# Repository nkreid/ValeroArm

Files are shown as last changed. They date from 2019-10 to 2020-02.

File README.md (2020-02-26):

# ValeroArm
I spent the summer of 2019 building a cost-effective, durable, and versatile tendon-driven arm. The motivation was to build an arm that had planar, universal, and rotational joints on a large scale. This design could then be scaled down to the size of fingers on the hand. We built and modeled a planar, two joint, three muscle system.

# Tendon Routing and Moment Arm Size Optimization
  A large focus was directed toward finding the optimal tendon routing for the arm. This was done in python by maximizing the radius of a circle inside the Feasible Force Set with the circle’s center located at the endpoint. The choice of a circle defined the maximum force the endpoint could exert in all directions. The routes were swept over the anatmical limits of the elbow (-10 degrees,150 degrees) and averaged over the range. This average force production was our metric we used to pick the most versatile route. We defined versatile as “producing the largest force in all directions, for every position.”
  
  For a two joint, three muscle this produces a 2x3 matrix with close to 800 combinations. Each row is a joint and each column is a muscle. The numbers one and negative one were used to denote the direction of angle change that a tendon could produce. Tendons can only act on a joint in one direction because muscles only contract and cannot extend. The possible R matrices were reduced to 14 by the following assumptions: 
    
    1.	Every row needs a positive and negative moment arm to move in both directions.
    2.	The top row cannot contain a zero because the current design of the arm does not 
        allow a tendon to reach the distal  joint without first touching the proximal joint. 
    3.	Matrices with the same columns in different orders are duplicates of each other. 
    
  Out of the 14 matrices, 10 produced numerical results with 2 routes clearly stronger than the rest. These two matrices were “opposites” of each other as shown in FIGURE. This optimal tendon routing is consistent with the routing chosen in (G2P Paper). This information was presented on a poster at the Keck School of Medicine’s summer undergraduate poster symposium. 
	
  The 14 feasible routes were then scaled to allow for moment arm differences between each muscle and joints. The 14 feasible routes were multiplied by almost 2 million scaling matrices by scalar multiplication.  These scaling matrices were all the variations of a 2x3 matrix containing the numbers between 0 and 1 (inclusive) with a 0.1 step (0,0.1,0.2,0.3…). By choosing a maximum of 1.0, these values are normalized by dividing all the values by the arm's largest moment arm. These new matrices were ran through the same optimization procedure as before and the top 100 matrices were kept. The results are as follows:
```
       MATRIX         Average Force Output
[[-1.   0.2  0.9]
 [-0.1 -1.   1. ]]  :: 2.3684792518615723
[[-1.   1.   0.4]
 [-0.6 -0.9  1. ]]  :: 2.369333267211914
[[-1.   0.9  0.4]
 [-0.6 -0.8  1. ]]  :: 2.369748115539551
[[-0.1 -0.9  1. ]
 [-1.   0.3  0.6]]  :: 2.3703784942626953
[[-1.  -0.1  1. ]
 [-1.   0.9  0.1]]  :: 2.3703880310058594
[[-0.1 -1.   1. ]
 [-1.   0.2  0.9]]  :: 2.3708009719848633
[[-1.   1.   0.1]
 [-1.  -0.5  1. ]]  :: 2.373188018798828
[[-0.1 -1.   1. ]
 [-1.   0.3  0.6]]  :: 2.376481533050537
[[-1.  -0.1  1. ]
 [-1.   1.   0.1]]  :: 2.3765554428100586
[[-1.   0.9  0.1]
 [-0.8 -0.5  1. ]]  :: 2.377281665802002
[[-1.   1.   0.2]
 [-0.8 -0.3  1. ]]  :: 2.377704620361328
[[-1.   0.1  1. ]
 [-0.1 -1.   0.9]]  :: 2.3780016899108887
[[-1.   0.1  1. ]
 [-0.2 -0.9  1. ]]  :: 2.3781371116638184
[[-1.   1.   0.2]
 [-0.6 -0.6  1. ]]  :: 2.37845516204834
[[-0.1 -1.   1. ]
 [-1.   0.3  0.7]]  :: 2.3785605430603027
[[-0.1 -0.9  1. ]
 [-1.   0.   0.9]]  :: 2.378894805908203
[[-1.   0.8  0.2]
 [-0.8 -0.4  1. ]]  :: 2.378972053527832
[[-1.   1.   0.2]
 [-0.8 -0.5  1. ]]  :: 2.378972053527832
[[-1.   1.   0.2]
 [-0.7 -0.4  1. ]]  :: 2.380239963531494
[[-1.   0.8  0.2]
 [-0.8 -0.3  1. ]]  :: 2.380913734436035
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
```

It is interesting to note that our best routes are not all ones and zeros as initially expected. However, the top 5 results are all very similar with minor deviations.

# Physical Design and Construction
  The first design of the arm was constructed together with Paris Hijali. It was made out of PVC and 3D printed components. While it was a solid proof of concept, there were many problems that arose. I addressed many of these problems in the second version. 
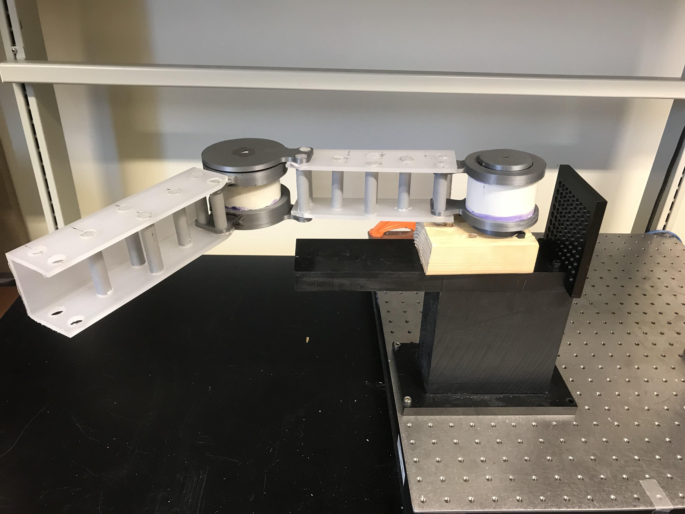
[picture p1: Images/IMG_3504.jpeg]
PVC Arm


  Version 2 was created using very modular parts which allowed for the arm to be modified depending on the task. Most of the parts were ordered from McMaster or ServoCity. This version of the arm included a planar elbow and shoulder joint along with a rotational pronation/supination joint in the forearm. At the end of the arm, there were three versions of a wrist-- ranging from zero to the two degrees of freedom that a real wrist has. We constructed the version with zero DOFs for the first phase of testing. The current hand we were using in the lab was underactuated and driven by two servos. There was a cavity created in the distal forearm to house the two servos needed to drive the hand. 
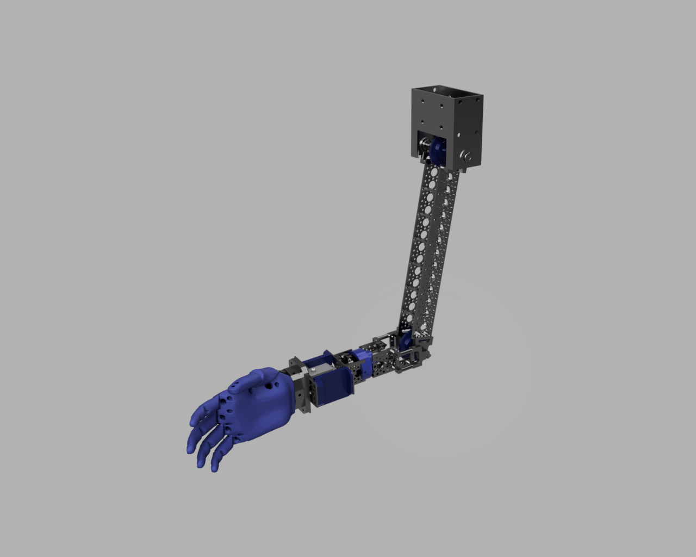
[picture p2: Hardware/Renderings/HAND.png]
Modular Arm
 

  We designed a multi-moment-arm (MMA) for a planar joint. It allowed multiple tendons to pass over the same joint with different moment arms. If I were to experimentally test the optimization that I presented above, I would create different MMA according to different routes. I would then put the endpoint of the arm into a device to measure the force. I could then sweep the elbow joint and measure the forces in different postures to see if it supports the data derived theoretically. 
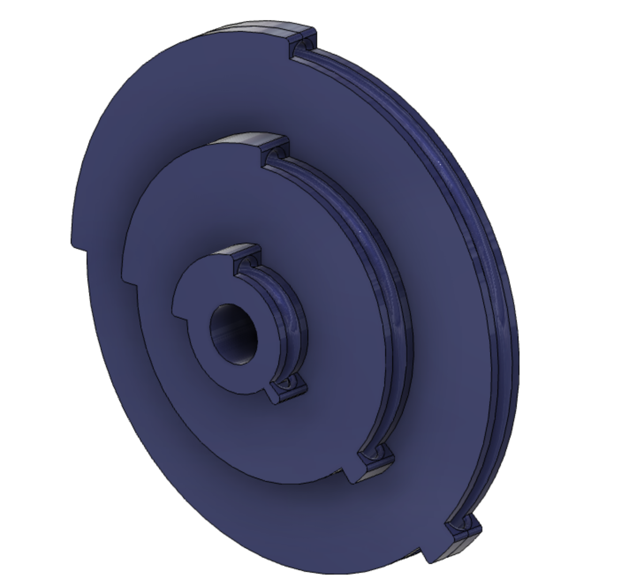
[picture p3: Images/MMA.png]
MMA


# Future Directions
All the code is linked on the GitHub for this page at https://github.com/nkreid/ValeroArm
In addition, all the CAD files are available on Fusion 360 under the project title 'HAND - BBDL'
If you need access to either please ask Suraj or Koby.

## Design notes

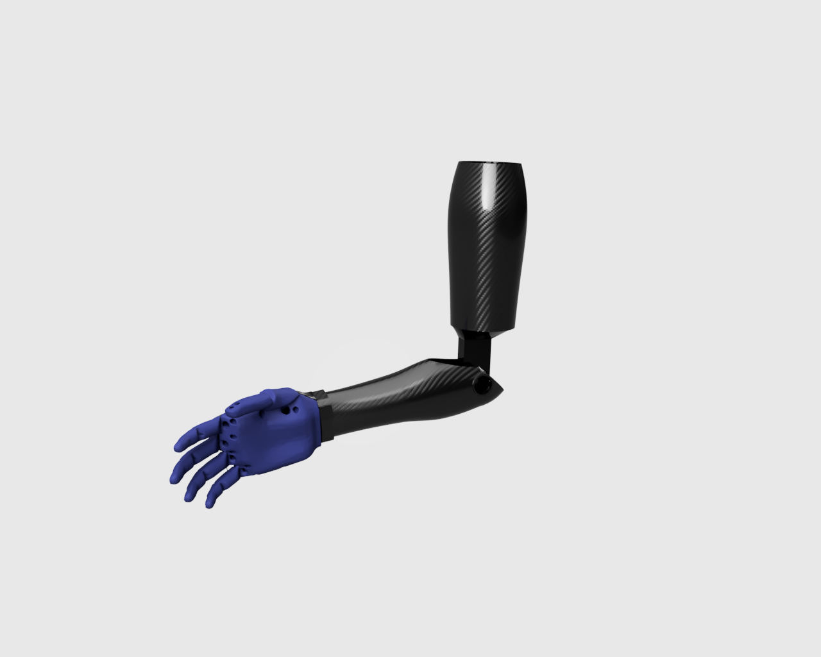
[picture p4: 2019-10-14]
Hardware/Renderings/Prosthetic/Custom_Forearm_2019-Jul-27_07-30-07PM-000_CustomizedView183382668_png.png

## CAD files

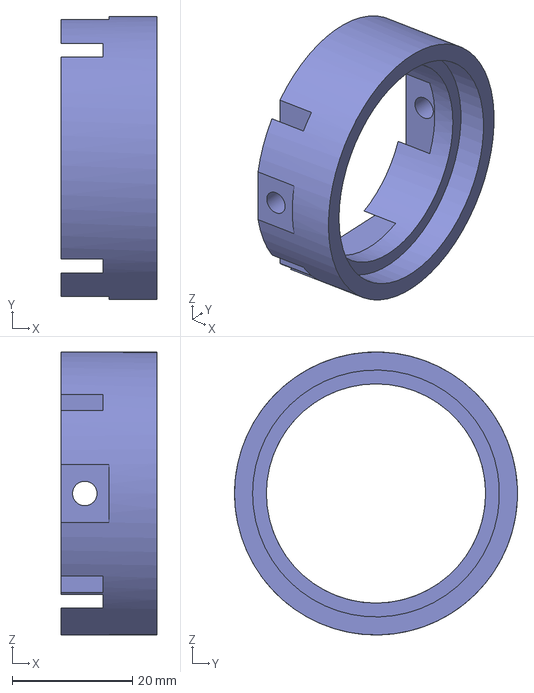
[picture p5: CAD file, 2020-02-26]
Hardware/Fusion Files/Rotation Joint_Outer Sleeve v1.step
16.0 x 47.0 x 47.0 mm

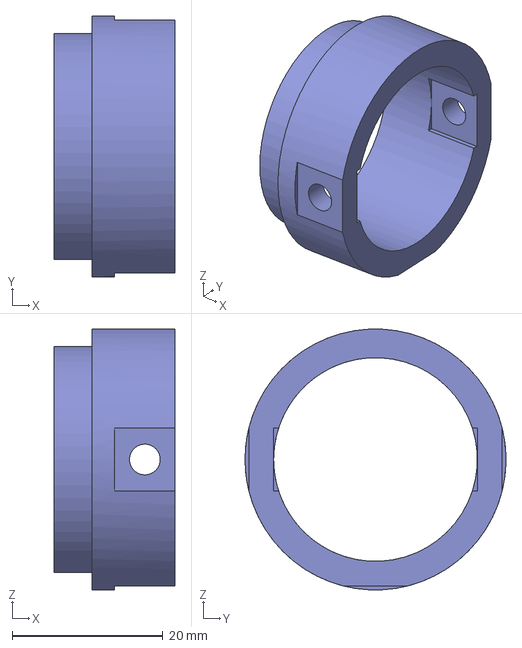
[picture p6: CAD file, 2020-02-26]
Hardware/Fusion Files/Rotation Joint_Inner Sleeve v1.step
16.0 x 34.6 x 34.5 mm

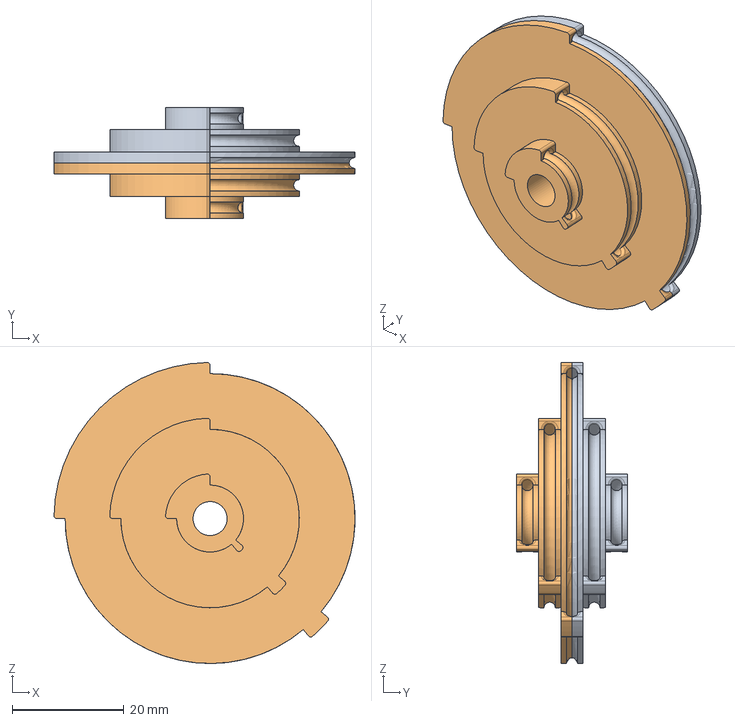
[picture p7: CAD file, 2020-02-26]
Hardware/Fusion Files/Multi Moment Arms (MMA) v5.step
54.0 x 20.0 x 54.0 mm

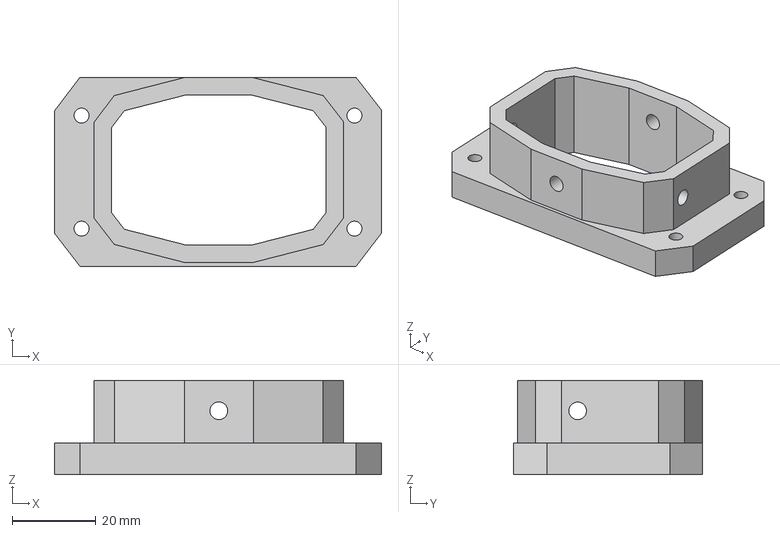
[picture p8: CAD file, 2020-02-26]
Hardware/Fusion Files/R_Ada_v1.1_Back_Cover_Hand Adapter v3.step
77.9 x 45.0 x 22.5 mm

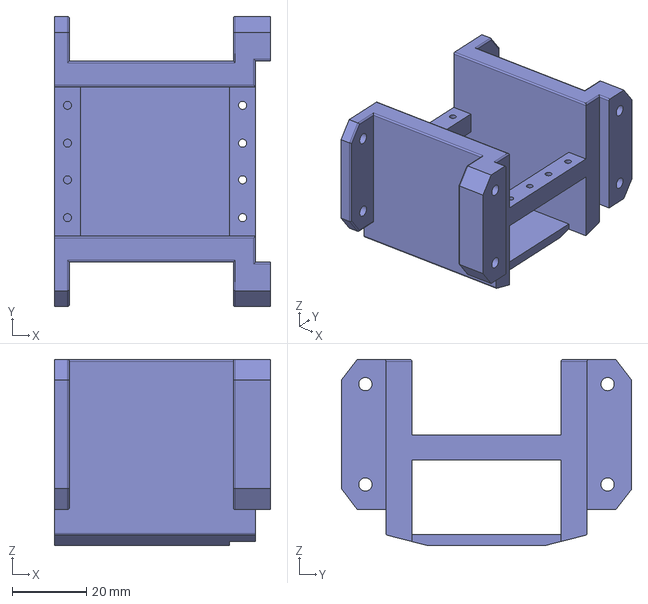
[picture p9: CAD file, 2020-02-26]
Hardware/Fusion Files/HAND v2_Servo Holder v3.step
58.0 x 77.9 x 50.0 mm

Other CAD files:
Hardware/Fusion Files/HAND v2_Servo Holder v3.f3d
Hardware/Fusion Files/Multi Moment Arms (MMA) v5.f3d
Hardware/Fusion Files/R_Ada_v1.1_Back_Cover_Hand Adapter v3.f3d
Hardware/Fusion Files/Rotation Joint_Inner Sleeve v1.f3d
Hardware/Fusion Files/Rotation Joint_Outer Sleeve v1.f3d

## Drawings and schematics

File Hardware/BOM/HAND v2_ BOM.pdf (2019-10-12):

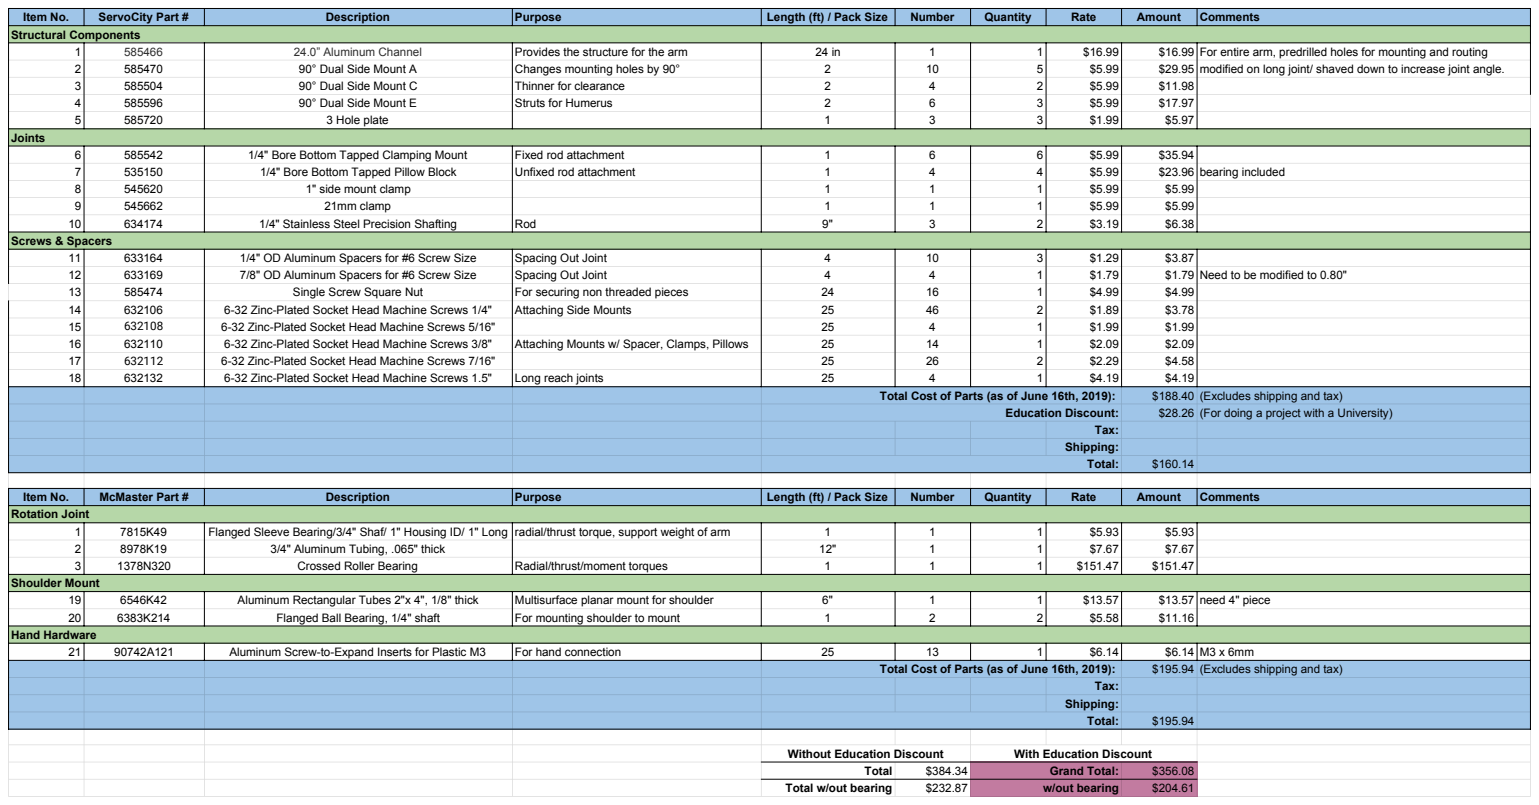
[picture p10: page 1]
Item No.; ServoCity Part #; Description; Purpose; Length (ft) / Pack Size; Number; Quantity; Rate; Amount; Comments; Structural Components; 24.0” Aluminum Channel; Provides the structure for the arm; For entire arm, predrilled holes for mounting and routing; 90° Dual Side Mount A; Changes mounting holes by 90°; modified on long joint/ shaved down to increase joint angle.; 90° Dual Side Mount C; Thinner for clearance; 90° Dual Side Mount E; Struts for Humerus; 3 Hole plate; Joints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

Humerus | | Proximal Forearm | short | long
Channel | 10.4" | 90° Dual Side Mount A | 4 | 4

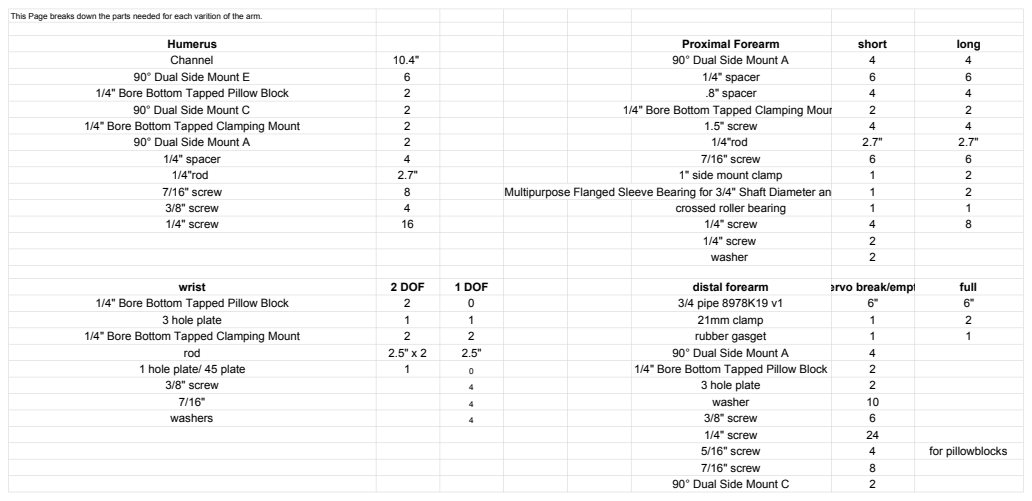
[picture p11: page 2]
90° Dual Side Mount E; 1/4" spacer; 1/4" Bore Bottom Tapped Pillow Block; .8" spacer; 90° Dual Side Mount C; 1/4" Bore Bottom Tapped Clamping Mount; 1.5" screw; 90° Dual Side Mount A; 1/4"rod; 7/16" screw; 1" side mount clamp; Multipurpose Flanged Sleeve Bearing for 3/4" Shaft Diameter and 1" Housing ID, 1" Long 1; 3/8" screw; crossed roller bearing; 1/4" screw; washer; wrist; 2 DOF; 1 DOF; distal forearm; servo break/empty; full; 3/4 pipe 8978K19 v1; 3 hole plate; 21mm clamp; rubber gasget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

This Page breaks down the parts needed for each varition of the arm.

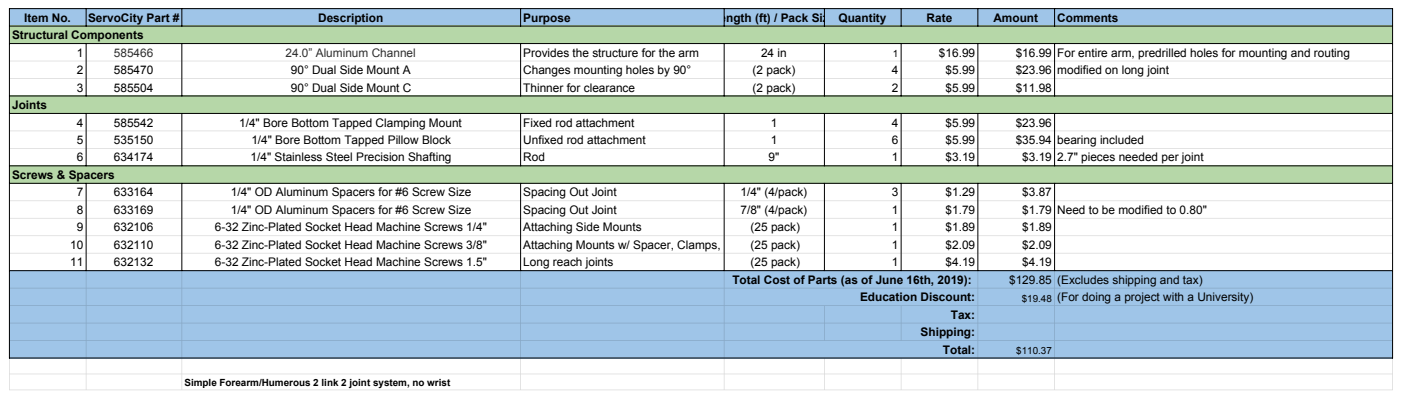
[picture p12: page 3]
Item No.; ServoCity Part #; Description; Purpose; Length (ft) / Pack Size Quantity; Rate; Amount; Comments; Structural Components; 24.0” Aluminum Channel; Provides the structure for the arm; For entire arm, predrilled holes for mounting and routing; 90° Dual Side Mount A; Changes mounting holes by 90°; (2 pack); modified on long joint; 90° Dual Side Mount C; Thinner for clearance; Joints; 1/4" Bore Bottom Tapped Clamping Mount; Fixed rod attachment; 1/4" Bore Bottom Tapped Pillow Block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

Simple Forearm/Humerous 2 link 2 joint system, no wrist

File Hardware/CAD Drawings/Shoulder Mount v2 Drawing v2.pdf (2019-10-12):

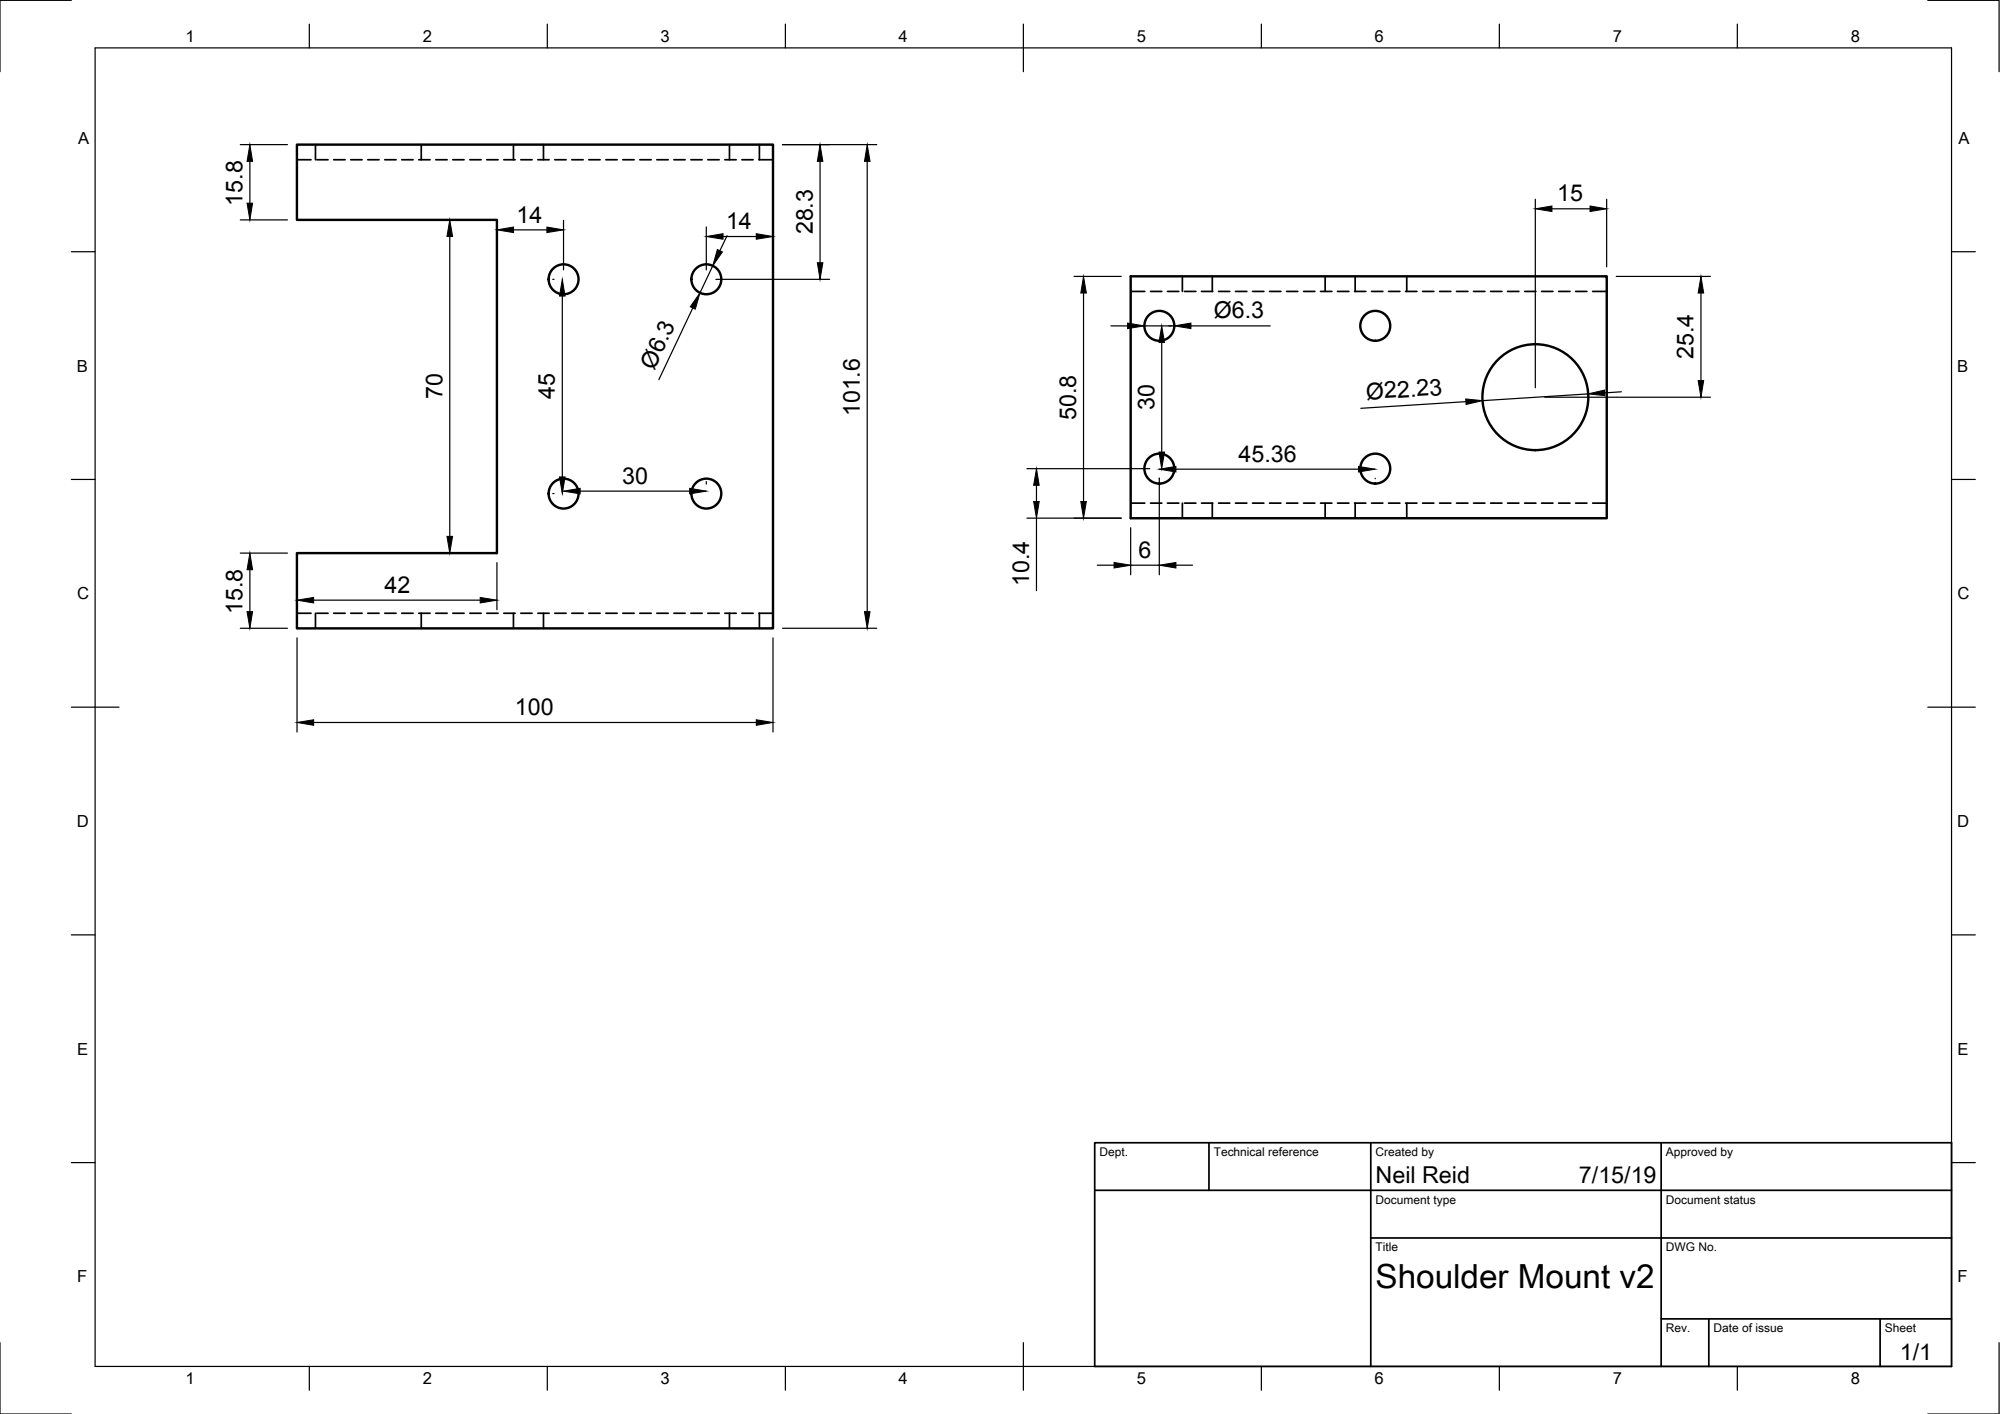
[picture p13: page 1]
Neil Reid 101.6

Dept. | Technical reference | Created by 7/15/19 | Approved by

Document type | Document status

Title Shoulder Mount v2 | DWG No.

Rev. | Date of issue | Sheet 1/1

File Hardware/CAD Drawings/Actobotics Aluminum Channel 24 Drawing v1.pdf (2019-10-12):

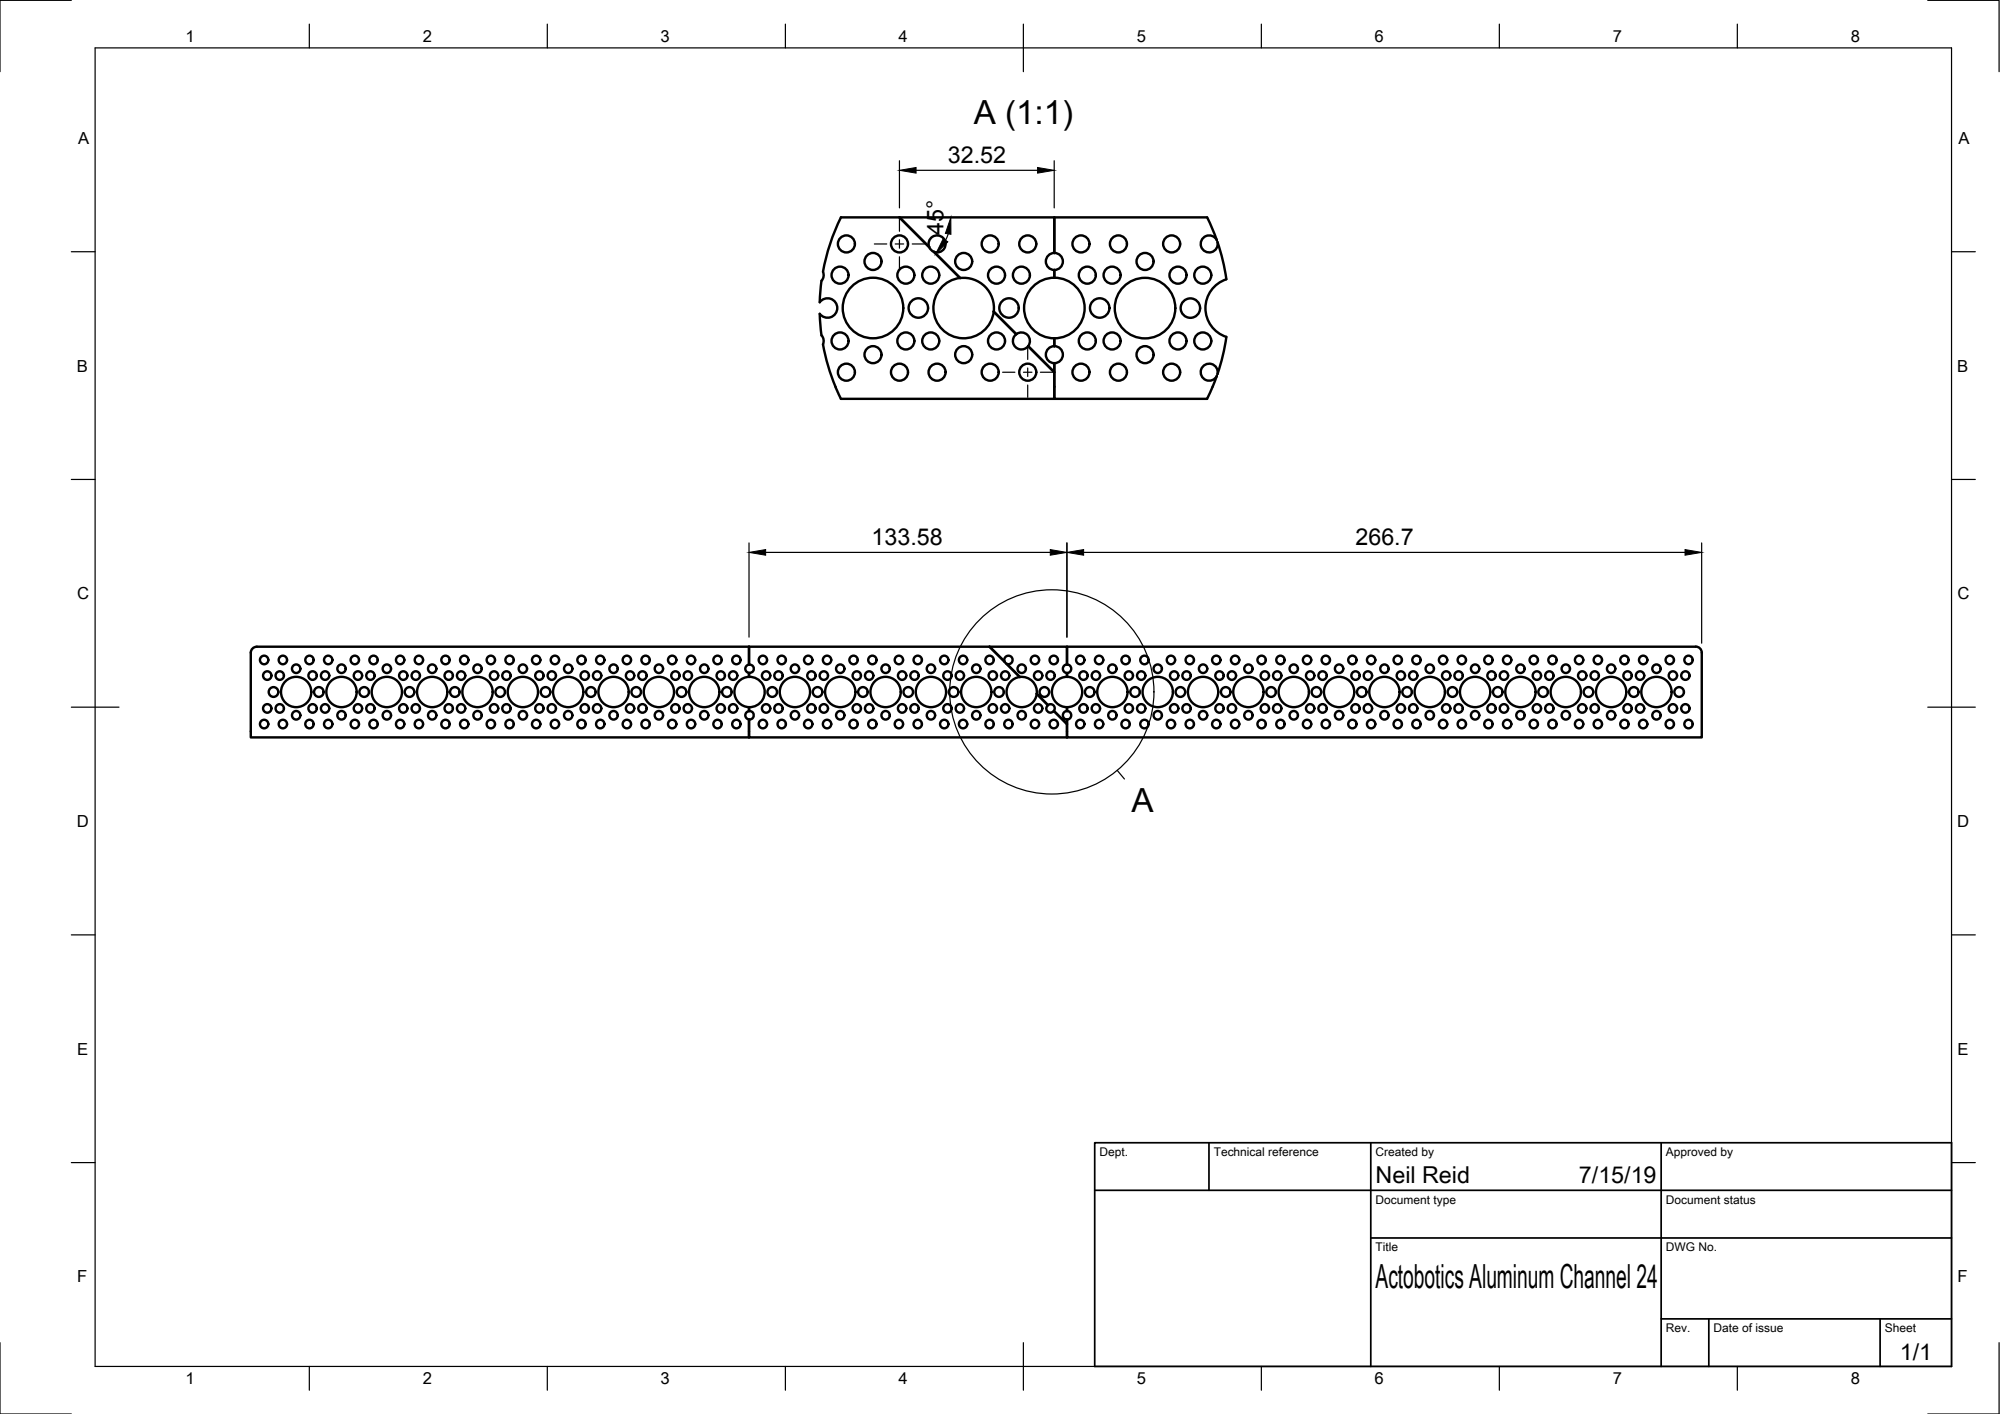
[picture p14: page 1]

Dept. | Technical reference | Created by Neil Reid 7/15/19 | Approved by

Document type | Document status

Title Actobotics Aluminum Channel 24 | DWG No.

Rev. | Date of issue | Sheet 1/1

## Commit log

2019-03-11 Add Limb Kinematics
    Add the Limb_Kinematics.py file to the repository. It contains a rotation, transformation, and geometric matrix function.
2019-03-12 Upload Symbolic Matrices
    Program outputs symbolic matrices for a n-joint system in 2-D. Contains functions for rotation matrices, transformation matrices, the Grasp (G matrix), and the Jacobian (J matrix).
2019-10-11 Moment Arm Scaling
2019-10-12 added BOM
2019-10-14 added fusion file for arm
2020-02-26 added fusion files
    [HAND v2_Servo Holder v3.f3d, HAND v2_Servo Holder v3.step, Multi Moment Arms (MMA) v5.f3d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]
